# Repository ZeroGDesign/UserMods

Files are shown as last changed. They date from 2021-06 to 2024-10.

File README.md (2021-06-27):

# ZeroG repository

Welcome to the [ZeroG](https://github.com/ZeroGDesign/Mercury) github repository. This is a place to share your awesome mods for the Mercury One and find useful resources from other ZeroG community members.

Check the  [`Mercury_One`](./Mercury_One) and [`Slicer_profiles`](./Slicer_profiles) folders for mods that apply to the [Mercury One](https://zerogdesign.github.io/index.html).

If you want to contribute to this repository check step by step guide in [How to contribute](./docs/how_to_contribute.md)

<a href="https://discord.com/invite/gzJP2s8" target="_blank">Discord Shield</a>

<a href="https://www.buymeacoffee.com/dutchdude" target="_blank">Buy Me A Coffee</a>

ZeroGDesign/UserMods is licensed under the
GNU General Public License v3.0<br><br>


Credits to [VoronDesign/VoronUsers](https://github.com/VoronDesign/VoronUsers)

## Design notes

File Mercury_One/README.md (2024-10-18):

# Mods

Printer mods for ZeroG 3D printers
Remember to update this README when uploading new mod!

## Directory structure

Create a folder containing your name (without spaces) and create a folder for your mod(s).

Suggested directory layout for your mod:
- `creator_name/`
  - `mod_name/`
    - `README.md` with a description, optionally build instructions and required parts
    - `stl/` folder with stereolithographical models, oriented correctly for printing
    - `cad/` folder with original design files (STEP, F3D, Scad, etc.) (optional)
    - `doc/` folder with supported documentation (optional)
    - `images/` folder with screen shots/renders/etc.

## Table structure

Update the following table with the information about your mod:
- Your name
- A link to your sub-folder
- A short description of your mod
- The build difficulty:
  - `:green_heart:` for :green_heart: (Easy)
  - `:blue_heart:` for :blue_heart: (Intermediate)
  - `:heart:` for :heart: (Advanced)

like so:
`
| Creator | [Mod title](link) | Description | Difficulty `

---

| Creator | Mod title | Description | Difficulty
| --- | --- | --- | --- |
| *creator_name* | [*Mod Title*](./creator_here/mod_folder_name) | *Example description (short).* |:green_heart::blue_heart::heart:
| ZeroG | [Spool Holder](./ZeroG/Spool_holder) | Its a spool holder... Its holds spools? | 💚
| aepkolol | [rPi 3.5 LCD mount](./aepkolol/rPi-3.5-LCD-mount) | Adafruit 3.5" TFT screen on the front | 💚
| bertoo1337 | [AfterBurner fan shroud](./bertoo1337/AfterBurner_fan_shroud) | Mercury branded fan shroud for the Voron AfterBurner toolhead | 💙
| cncplasticfactory | [EVA KW10 X-axis endstop and bumpstop](./cncplasticfactory/EVA_KW10_X_endstop) | An X-axis endstop mount and bumpstop to use a KW10 microswitch with the EVA hotend | :green_heart:
|  | [KW10 enlarged Y-axis endstop mount](./cncplasticfactory/KW10_enlarged_Y_mount) | A modified and slightly enlarged Y-axis endstop mount for use with KW10 microswitches | :green_heart:
|  | [MGN12 Y-axis bumpstop endcaps](./cncplasticfactory/MGN12_linear_rail_bumpstop_caps) | Delightful bumpstops caps for Y-axis MGN12 linear rails | :green_heart:
| djsplice | [EVA - Biqu H2 Mount](./djsplice/EVA-Biqu-H2) | EVA Faceplate and fan shroud for the Biqu H2 hotend/extruder | 💚
|  | [Static Cooling System](./djsplice/SCS) | Static Cooling System for the Mercury 1.1 based on VzBoT RSCS system | 💚
| maze | [2020 endcap](./maze/2020-endcap) | Zero G branded 2020 endcap | :green_heart:
| OhDeeEsTee | [Inverted XY Bridge](./OhDeeEsTee/Inverted_XY_Bridge) | inverted cable chain mount | :green_heart:
| Rudra | [X Extrusion Squaring Tool](./Rudra/X_Extrusion_Squaring_Tool) | Simple tool to square the x extrusion to the frame | 💚
|  | [Belt Tensioning Tool](./Rudra/Belt_Tensioning_Tool) | Simple tool to ensure a 150mm distance from idler to idler for easy belt tensioning | 💚
| DrPeterPlastic | [Wago4-Mount](./DrPeterPlastic/Wago4-Mount-Hydra)  | Mount for 4 Wagos on Hydra | 💚
| Vengeful | [Klicky Mount](./Vengeful/Klicky_Bracket) | E5 Plus Mounting Bracket for Klicky mod| 💚
|  | [Standalone Knob Tensioner](./Vengeful/Standalone_Knob_Tensioners) | Knob Tensioners for Mecrury Printers| 💙
| hrt_plk | [MGN9H gantry](./hrt_plk/gantry-mgn9h) | Custom parts to replace y axis from MGN12 to MGN9 | 💚
| JohnJohnGib | [ZeroG frame corner braces](./Tomadoggy/ZeroG_Frame_Braces) | Its a spool holder... Its holds spools? | 💚

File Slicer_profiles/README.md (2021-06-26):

# Slicer profiles

Slicer profiles for ZeroG 3D printers, separated by slicer.
Remember to update this README when uploading new slicer configurations!

## Table structure

Update the following table with the information about your mod:
- Your name
- A link to your sub-folder
- A short description of your slicer config
- The printer compatibility. Use `:heavy_check_mark:` for :heavy_check_mark: and`:x:` for :x:

like so:
`
| Creator | [Config Title](link) | Description | :x: | :x: | :x: | :x: |`

---

| Creator | Config title | Description | PrusaSlicer | SuperSlicer | Cura | Simplify3d|
| --- | --- | --- | --- | --- | --- | --- |
| DutchDude| [SuperSplicer high speed](./DutchDude) | Personal config high speed quality parts | :x: | :heavy_check_mark: | :x: | :x: |

---

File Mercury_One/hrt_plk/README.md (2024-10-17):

## Gantry MGN9H rails
  - Redesigned from original MGN12H
  - 4 bolts
  - successfully assembled

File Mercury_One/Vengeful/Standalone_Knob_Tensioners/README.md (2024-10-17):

# Standalone Knob Tensioners

This mod is designed to provide a simple and sturdy solution for tensioning belts on the Ender 5 Plus(Need confirmation for the Ender 5) Mercury 1 and Mercury 1.1 Systems

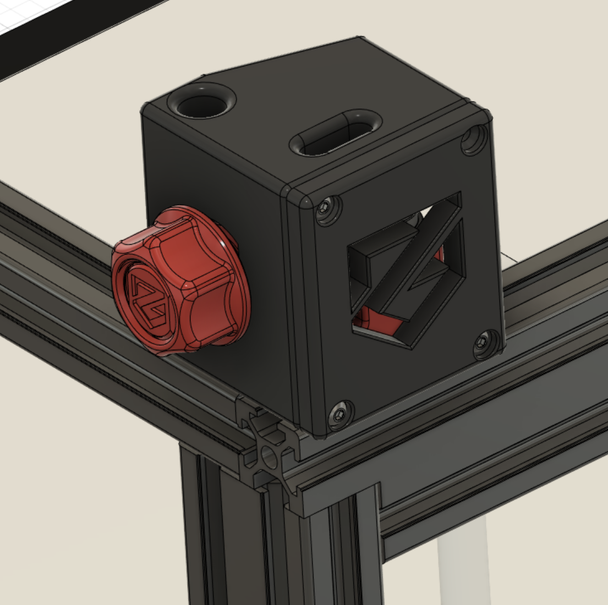
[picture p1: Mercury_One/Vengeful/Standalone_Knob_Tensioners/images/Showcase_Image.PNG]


## Description

This Mod is derived from the enclosure project I am currently working on (Jan-2023). In order to provide a version that can be used by the entire Mercury community. I have forked the design and will upload the enclosure version once I am done. This was inspired by the Voron V0. This provides a sturdy solution for tensioning your belt while maintaining a design that allows clearance for an enclosure.  

## Dependencies

* **Please print in ABS or ASA**
* Due to the tight clearances of a part like this, I recommend this part be printed on a properly calibrated printer
* I **Do not** recommend scaling the parts via a slicer as you may have issues with fitment

## Bill of Materials
Item Name | Quantity | Notes
| :--- | :---: | :---
M5x12mm BHCS | 2 | Needed for Rear Mount
M5x25mm BHCS | 2 | Needed for Inside Mount
M3x6MM BHCS | 8 | Needed to secure lid
M3x4mmx5mm Heatset Inserts | 8 | Needed to secure lid
M5 T-Nut | 6 | You should have at least 4 existing T-nuts from the Original BOM
M5x20mm SHCS | 2 | From Original BOM
M5x30mm PIN | 2 | From Original BOM
M5x1mm Shim | 4 | From Original BOM
F695 Bearing | 4 | From Original BOM

## Installation

### Step 1 - Install Heatset Inserts

* Install the Heatset inserts with a soldering iron for both the Left and Right Frame printed parts
* Total amount of Heatsets to install is **8**
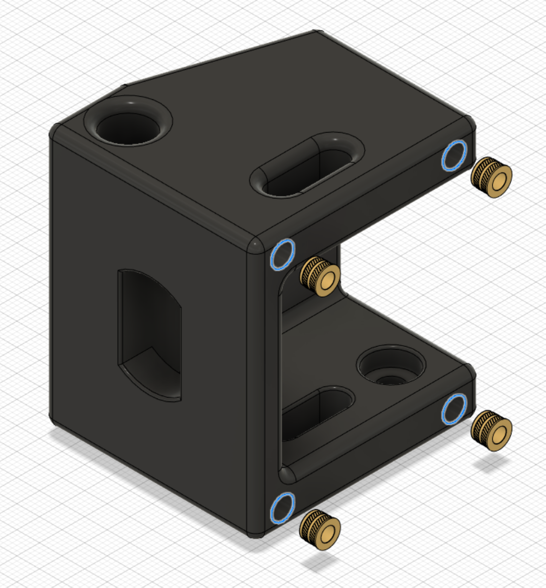
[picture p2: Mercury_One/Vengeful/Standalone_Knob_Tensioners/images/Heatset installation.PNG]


### Step 2 - Mount Frame to Extrusions

* Install the T-Nuts on both sides of the extrusion frame
* Total amount of T-Nuts to install is **6**
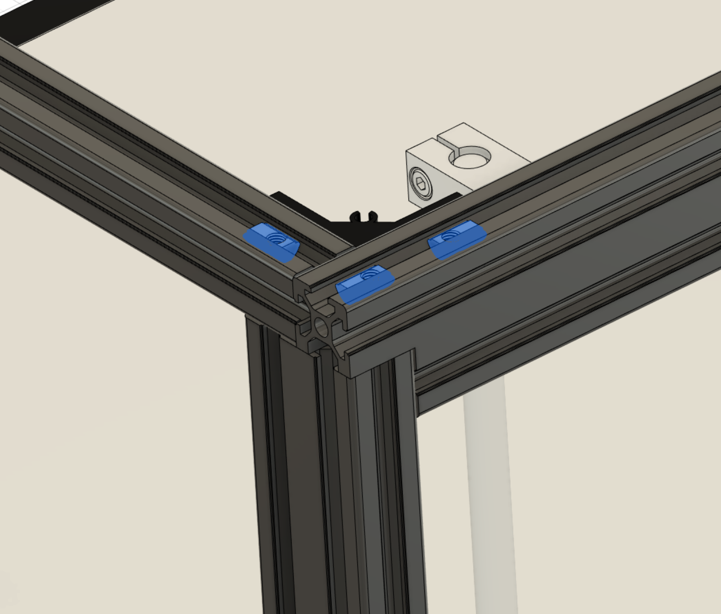
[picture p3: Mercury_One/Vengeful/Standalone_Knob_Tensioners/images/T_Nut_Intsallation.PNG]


* Install the M5x12mm BHCS at the Rear Mount hole
* Install the M5x25mm BHCS at the Inside Mount hole (This is a longer bolt to provide more structural rigidity)
* Repeat these steps on the other side as well
* Total amounts 
   * M5x12mm BHCS quantity of **2**
   * M5x25mm BHCS quantity of **2**
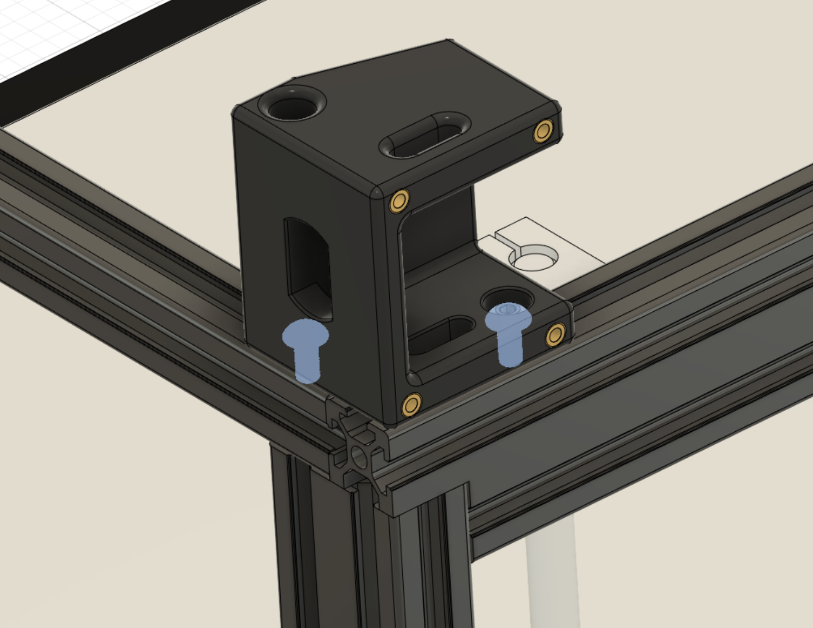
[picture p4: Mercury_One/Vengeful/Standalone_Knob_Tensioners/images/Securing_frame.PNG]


### Step 3 - Install Bearing Stack

* Install the bearing stack as prescribed in the original instructions for the Mercury Printers
* At this time you should insert the M5x20mm SHCS since the bolt will be held captive once the tensioner is inserted to the frame
* Repeat this process on both sides
* Total amounts 
   * M5x20mm SHCS quantity of **2**
   * M5x30mm PIN quantity of **2**
   * M5x1mm Shim quantity of **4**
   * F695 Bearing quantity of **4**
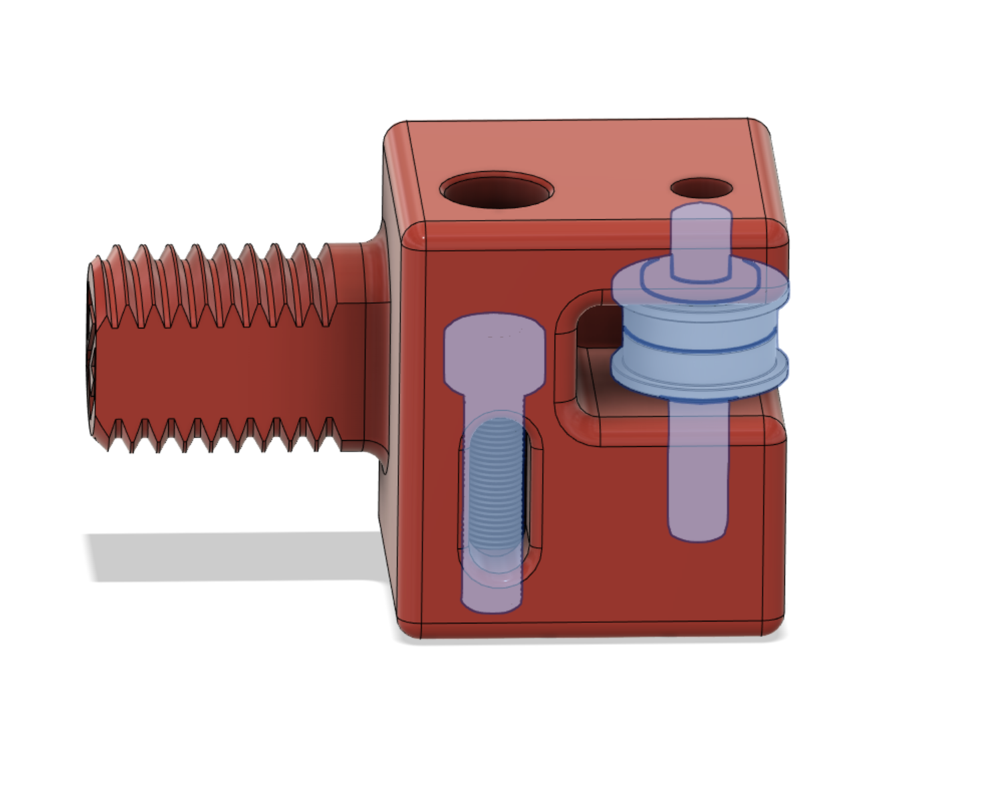
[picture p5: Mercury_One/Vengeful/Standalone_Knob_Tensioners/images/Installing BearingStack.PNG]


### Step 4 - Install Belt

* If this is a new build, follow the steps prescribed in the original instructions for the Mercury Printers
* if this is a retrofit, you will need to install as pictured below
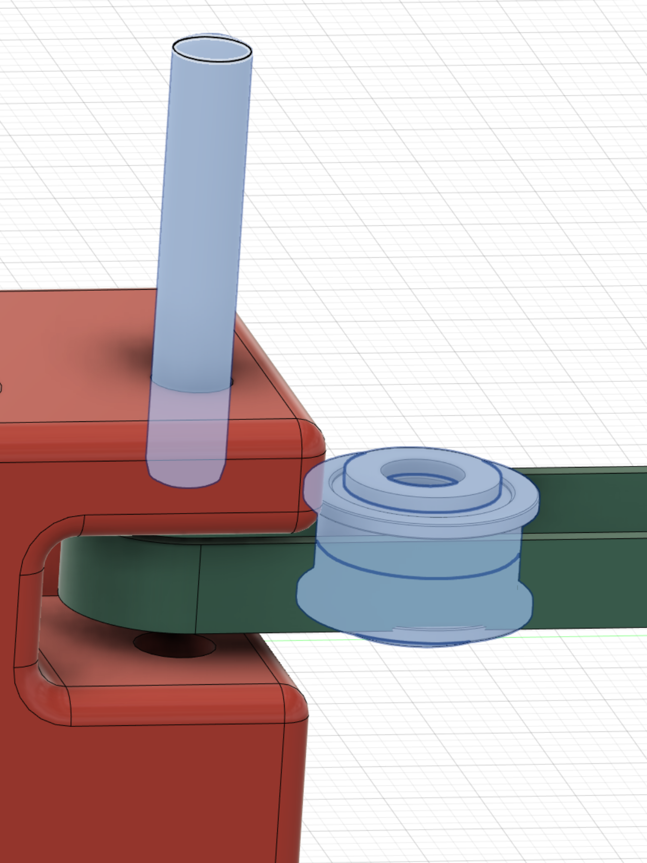
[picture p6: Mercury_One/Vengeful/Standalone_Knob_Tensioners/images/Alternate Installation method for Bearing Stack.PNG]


### Step 5 - Install Tensioner

* Slide in the tensioner to the frame
* Attach the M5x20mm SHCS to the T-Nut but **Do Not** fully tighten
* **Note** - the M5x20mm SHCS may catch on the initial hole
   * The Stadium Shaped Slot can be used to lift the bolt
   * This slot also exists in case you need to uninstall the tensioner - *since it will be captive once fully inserted*
   * A pick and hook can be used for this or a small screwdriver
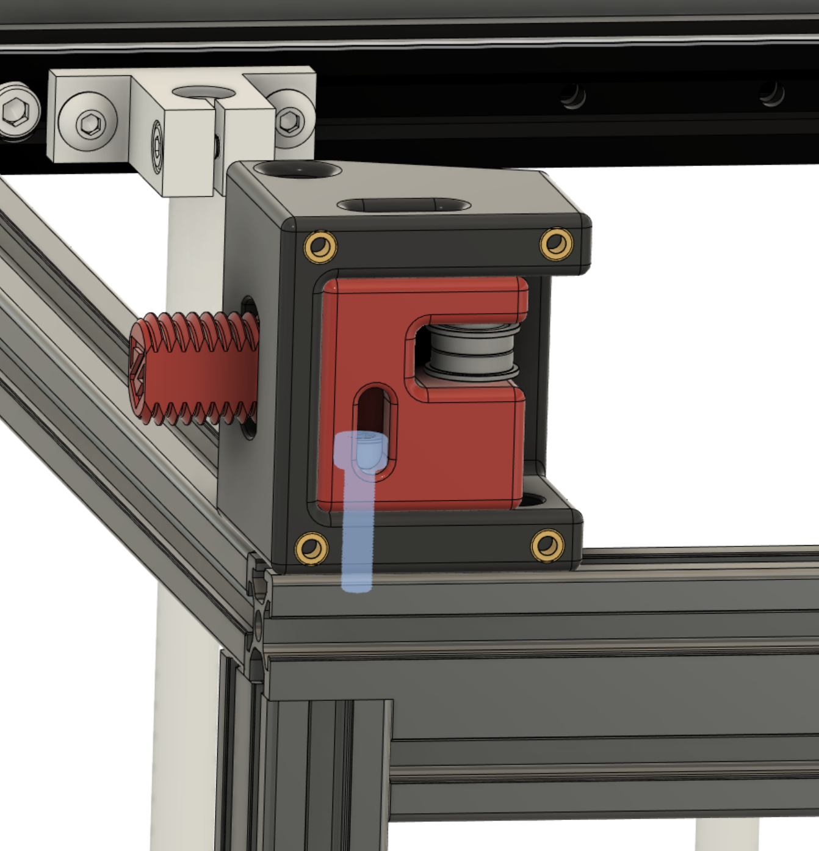
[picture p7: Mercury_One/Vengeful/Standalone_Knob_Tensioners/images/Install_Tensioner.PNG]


### Step 6 - Install Knob

* Install the knob but **Do Not** fully tighten until everything is installed 
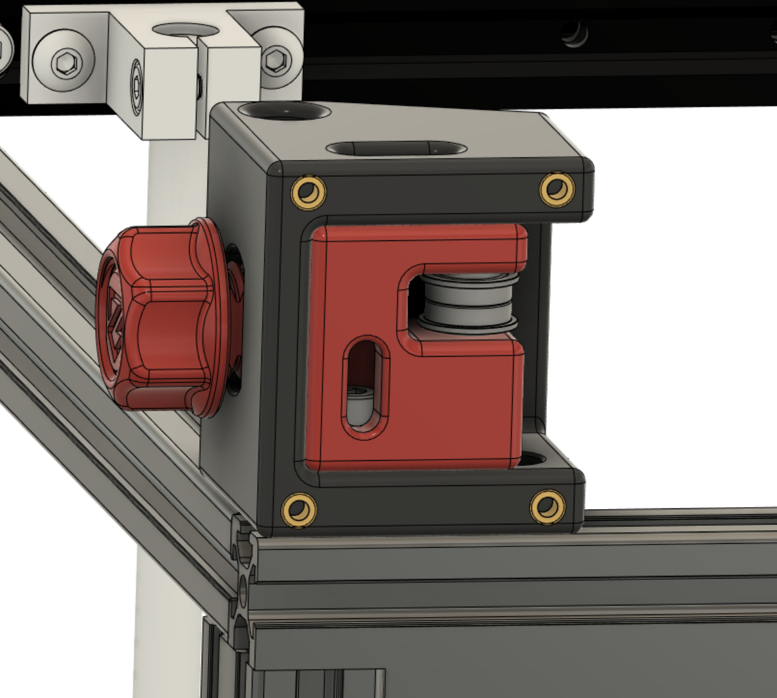
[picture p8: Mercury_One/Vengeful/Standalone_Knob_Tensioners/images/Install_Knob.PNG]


### Step 7 - Install Lids

* Install the lids on the sides of the frame
* Use the M3x6MM BHCS screws to secure the lids
* Total amount of M3x6MM BHCS screws to install is **8**
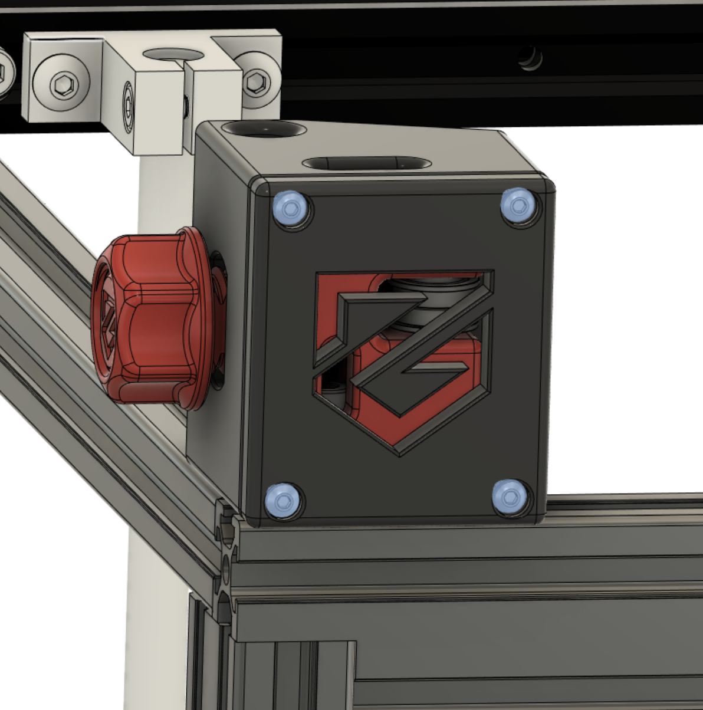
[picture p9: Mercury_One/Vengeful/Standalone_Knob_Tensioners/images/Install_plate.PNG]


## How to use

* Tension using the Knob
    * Ensure you are tensioning equally on both sides i.e 1/8th turn on each side simultaneously
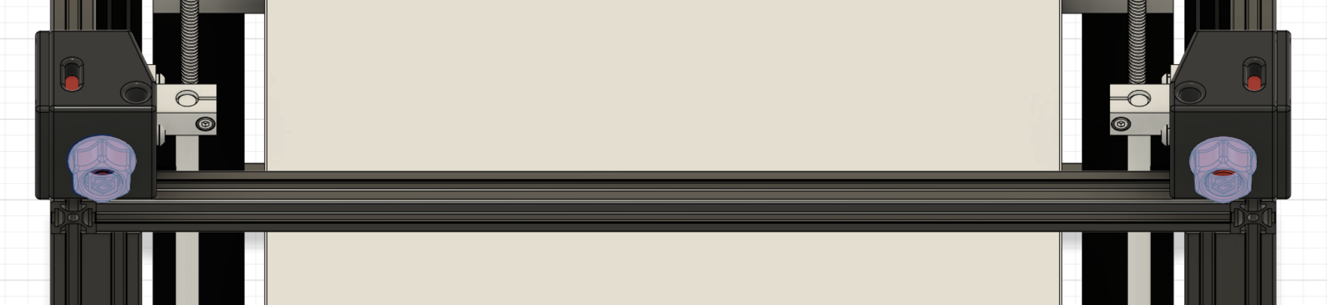
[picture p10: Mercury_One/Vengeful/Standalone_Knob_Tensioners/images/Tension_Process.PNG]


* Lock using the internal bolt inside the Stadium Shaped Slot
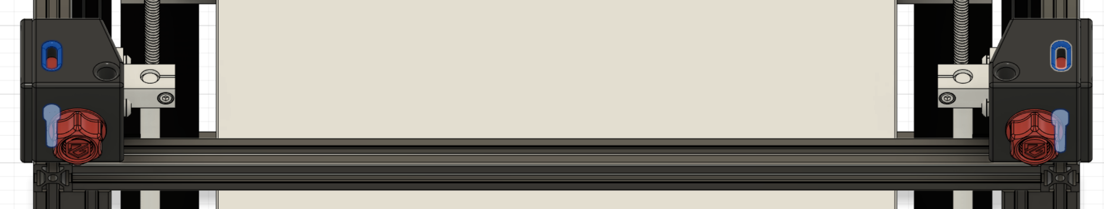
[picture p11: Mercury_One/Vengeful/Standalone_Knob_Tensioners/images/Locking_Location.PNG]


## Help

* Please reach out to me directly on discord if you have any issues or suggestions for this Mod 

## Authors

Vprince099 aka Vengeful Discord - Vengeful#8648

## Version History
    
* 0.1
    * Initial Release

## License

This project is licensed under the GNU GENERAL PUBLIC LICENSE - see the LICENSE.md file for details

## Acknowledgments

* ZeroG - Original Towers used to expand upon [Link to Project](https://github.com/ZeroGDesign/Mercury.git)
* Voron Design - V0 Team for Knob and Thread Appendage [Link to Project](https://github.com/VoronDesign/Voron-0.git)

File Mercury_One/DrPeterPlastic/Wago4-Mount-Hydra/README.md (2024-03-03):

Mount for 4 Wago connectors instead of 3

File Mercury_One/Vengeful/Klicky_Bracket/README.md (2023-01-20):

Intro:

This is dsigned for the Ender 5 Plus on the Mercury One System using a Stealthburner

Materials:

  M5x10 BHCS Q=2

  M5 T-Nut Q=2

  M3x4x5 Heatset Insert Q=2

Credit:
  
This is meant to be used with Klicky by jlas1 https://github.com/jlas1/Klicky-Probe.git

Images - 
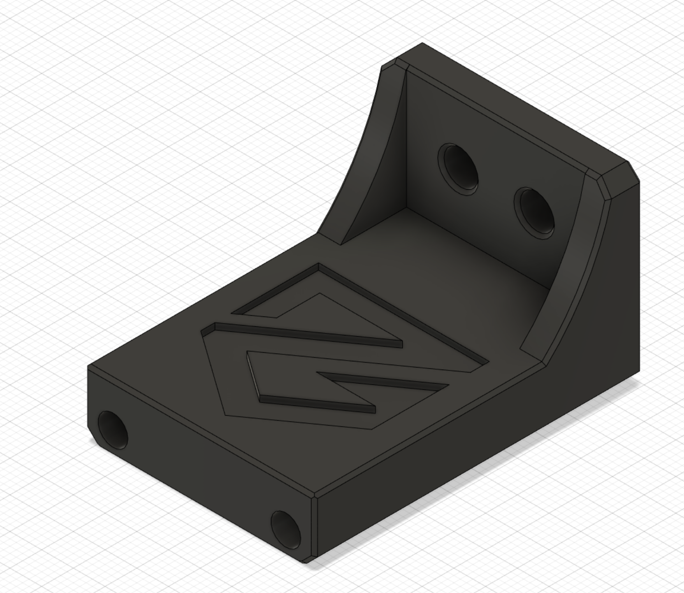
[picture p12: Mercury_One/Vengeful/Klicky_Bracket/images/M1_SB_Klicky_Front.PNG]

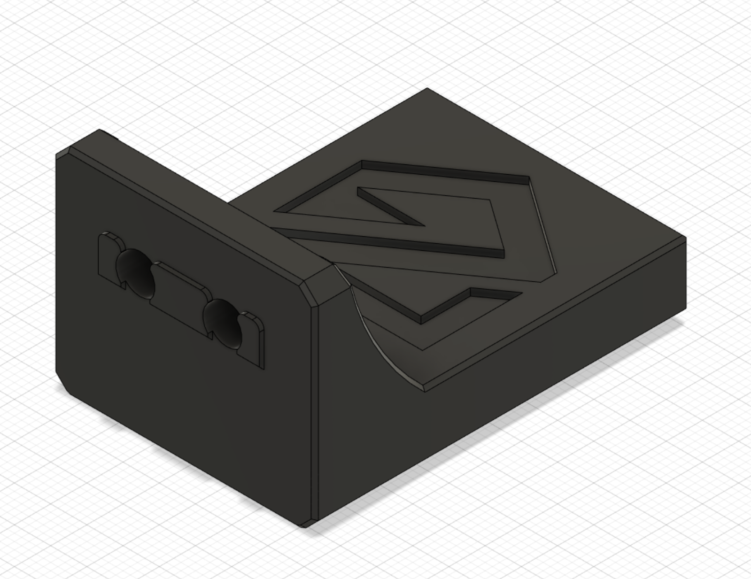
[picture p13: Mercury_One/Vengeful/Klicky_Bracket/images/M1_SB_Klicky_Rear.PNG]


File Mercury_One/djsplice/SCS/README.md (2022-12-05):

# Super Cooling System
This work is based on the [VzBoT RSCS system](https://grabcad.com/library/rscs-for-vzbot-1). Big thanks to the VzBoT crew, especially [Simon Vezina](https://grabcad.com/simon.vezina-2) for providing all of the CAD drawings and awesome videos for information, inspiration, and acceleration!

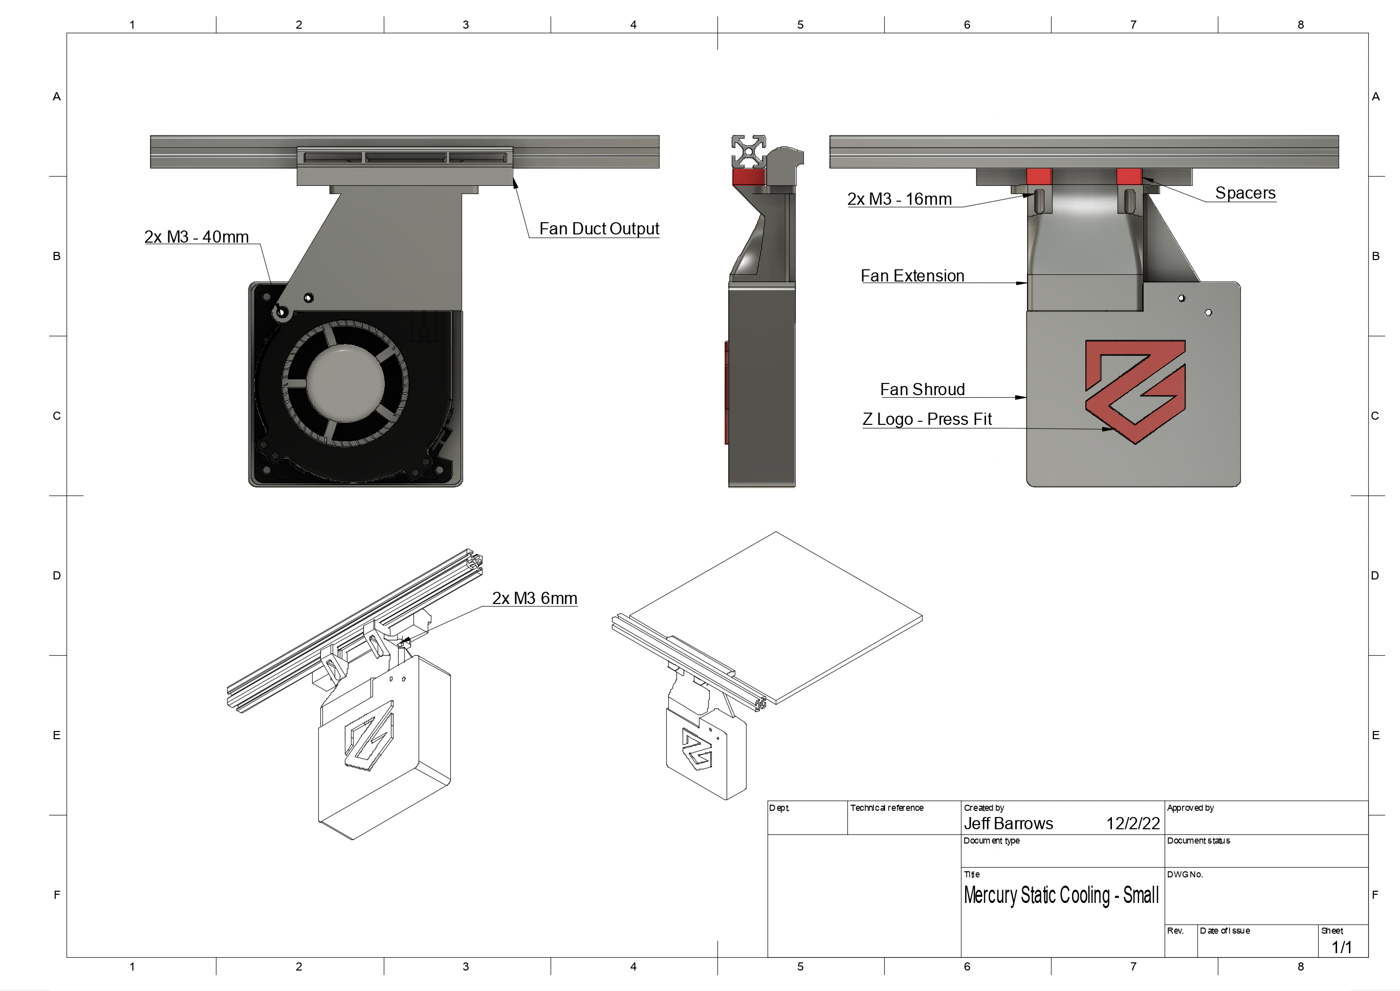
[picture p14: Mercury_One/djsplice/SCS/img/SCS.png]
Much SCS


## Release History
* 12/04/22 - Improved fan bracket airflow, and eliminated the need for the extension. Made shorter duct and increased inner cavity for improved airflow. Added a 'press-fit' Z for some flair.
* 7/11/22 - Updated fan bracket and shroud to cover more of the fans output. Increase overall fan bracket thickness improving mounting stability. Thanks to dansxmods#0246 (ZeroG Discord Server) for the suggestion!
* 5/26/22 - Initial Release

## What's SCS?
This is a system that's meant to cool top layer 3D printed extrusions quickly, helping you up the brrrr with better quality prints.

### What's the problem?
I found that as I tried to print at the higher end of my printers mechanical and extruder capabilities inevitably my print quality would suffer.  Especially challenging were overhangs, even 45 degree outer layers, and models with short layer print times (smaller single parts).

I moved to a dual 5015 cooling setup (EVA) for my part cooling which helped though at higher volumetric flows (~17mm3/sec), certain model features would become problematic (Benchy bow sag, ~45-50 degree overhangs in vase mode would deform at moderate speed, etc... ).

After watching and tuning for these scenarios it became clearer that cooling solutions that travel with the hot end have their limits. I think the main challenge is in that when printing at low layer times (<3sec), the fan ducts are generally not providing adequate cooling to the parts top layer surface because the hot end cooling fan is directly focused over the traveling nozzle.

More science necessary, though I believe cooling time could be calculated for a given material - helpful in determining quality print speed.

### Why try the SCS?
**First** I want to mention that the only reason I have this cooling problem is largely due to the [Zero-G Mercury project](https://github.com/ZeroGDesign/Mercury). By converting my heretofore fairly well tuned Ender 5 Pro printing at ~75mm/sec into something more 'moderately dangerous' - currently approaching 350mm/sec and 40mms3 volumetric flow.

After watching the [VzBoT video](https://youtu.be/65FVQ1jArME) on cooling solutions I was convinced to try this myself.

My hypothesis is that by adding additional top layer cooling, you'll be able to achieve higher speed/higher quality 3D prints.

If you're game, help me evaluate!

## SCS Parts, Printing, Installation
All printed files are found in the STL folder, CAD files *soon

This design works for the Ender 5 Pro, just fits between the top 2020 extrusion and a 300mm bed. If you have a smaller bed, or the Ender 5 Plus it should fit, though for the plus it may be a bit too far away from the bed, or not provide great part coverage... Drop an issue in Github if you get a chance to test it!

You will need M3 screws, 2 fans, and the ability to print 15mm overhangs clearly - you can do it - or your money back!   

### Hardware
* 2x 120x32 centrifugal fans - make sure they match the voltage and pin configuration your board can work with!
 * Ability to crimp, solder, or otherwise connect the fans to your 3D printer controller board
* Various M3 bolts/nuts:
 * 2x 40mm bolts to affix fan and shroud to mount
 * 2x 6mm M3 bolts to connect the fan shroud to the fan extension
 * 2x 16mm M3 bolts to connect the entire system to the underside of 2020 Aluminum extrusion
* Roll In Spring T-Nuts for mounting the blower to the top 2020 extrusions-  - something like [these](https://8020.net/fasteningmethods/hardware/tnuts/rollin/rollintnutwithballspring.html)

### Printed Parts
I recommend using the the following print settings:
* 3 Perimeters and 4 bottom/top solid layers
* 40% infill

All printed parts are included in the STL folder - there are 5 parts:

* [Fan Duct.stl](stl/Fan_Duct.stl)
* [Z-Insert.stl](stl/Z-Insert.stl)
* [Fan Bracket.stl](stl/Fan_Bracket.stl)
* [Fan Shroud.stl](stl/Fan_Shroud.stl)
* 2x [Spacers.stl](stl/Spacers.stl)

### Installation
1. Thread the M3 6mm screws that will be used to attach the fan duct, let the screws protude slightly from the top so it's easier to mount the duct later. The screws will thread directly into the duct housing - no nuts necessary.
1. Insert the M3 16mm screws that will be used to mount the system to the underside of the 2020 extrusion, thread the t-nuts
1. Using roll-in t-nuts will allow you to tilt the duct and get them inserted under the 2020 extrusion
1. Center the duct so that it's in the middle of your print bed
1. Once the duct is hanging from the 2020 extrusions, insert the spacers between the the extrusion and the duct mount, and tighten the bolts
1. Mount the Fan Duct Output on top of the Fan Extension.
3. Mount the fan and the shroud

The base of Fan Duct Output should align with the base of your print bed - the idea is for the air to blow onto the top layer of your print, if it's too high above the bed, it won't be as effective.

You may need to adjust the height of the spacers to achieve optimal alignment for your printer.
[TODO] Add a few more spacer sizes to accommodate

### Klipper gcode macro example
Configure Klipper to control the fans and expose a GCode macro so it can be controlled by your slicer.

#### Klipper Fan configuration
```
[output_pin Bed-Blower-R]
# BED BLOWER RIGHT
pin: PD12
pwm: true

[output_pin Bed-Blower-L]
# BED BLOWER LEFT
pin: PD13
pwm: true
```

#### Klipper GCode Macro
```
[gcode_macro BED_BLOWER]
gcode:
    # Use a default fan speed to off - expecting an INT as input
    {% set S = (params.S)|default(0)|float %}
    {% if S > 0 %}
        {% set S = (S/100) %}
    {% endif %}
    SET_PIN PIN=Bed-Blower-R VALUE={S}
    SET_PIN PIN=Bed-Blower-L VALUE={S}
```

#### Klipper Custom M106 Macro
This macro will set your SCS Fans to the same value your slicer sets the part cooling fans to, making it more dynamic. There are probably some advantages to having an 'always on' static setting, vs a dynamically adjusted setting such as this.

```
[gcode_macro M106]
rename_existing: M106.1
gcode:
  M106.1 { rawparams }
  {% set bed_blower_speed = params.S|float * 100/255 %}
  SET_PIN PIN=Bed-Blower-R VALUE={ bed_blower_speed/100 }
  SET_PIN PIN=Bed-Blower-L VALUE={ bed_blower_speed/100 }
```

### SuperSlicer custom gcode integration
In order to automatically turn on the SCS fans at a specific layer height, you need to add some custom `Before Layer Change G-code` section under the 'Printer Settings' in SuperSlicer.

```
; Set SCS fans to 40% when you reach the 3rd layer
{if layer_num == 2} BED_BLOWER S=40{endif}
```

## Known Issues

### Fan Duct Outlet
* Lots of bridging in this print!!  I tried to keep the bridge distance low, around 15mm or so... It's a bummer, but hopefully it's doable.

### Fan Bracket
* There are only 2 points to connect the fan to the bracket and it isn't as secure as I'd like. I'll probably look to add another mount point and potentially strengthen the hole on the point of the triangle...

## Experiments
Here are some pictures of benchys printed using the same g-code, but with  different cooling solutions.

Slicer configuration
2 Perimeters, 3 Top/Bottom solid
.2mm layer height
18% gyroid infill
Internal Perimeter Speed 250mm/s - External - 125mm/s
Max Volumetric Speed 43mm/s

1. Single 5015 Part cooling Fans at 100%
1. Dual 5015 Part cooling Fans at 100%
1. Dual 5015 Part cooling fans at 100% plus SCS fans at 100%

My interpretation of these results:
* Short layer times require increased cooling capacity
* Certain features (like overhangs) will degrade more than others when cooling isn't sufficient
* Layer times and cooling requirements are correlated - faster layer times will require more Cooling
* Prints that have more surface area may have a bit more time to cool before the next layer is applied, however, nozzle based cooling solutions will be less effective because they are only in a position to cool a section for a very short amount of time (as the filament is extruded from the nozzle)
* Smaller prints can benefit somewhat from increased nozzle based cooling systems because the ducts are likely to cover more surface area of the print for a more sustained period of time. Unfortunately smaller parts will likely have very short layer times and nozzle based cooling will probably not be sufficient   

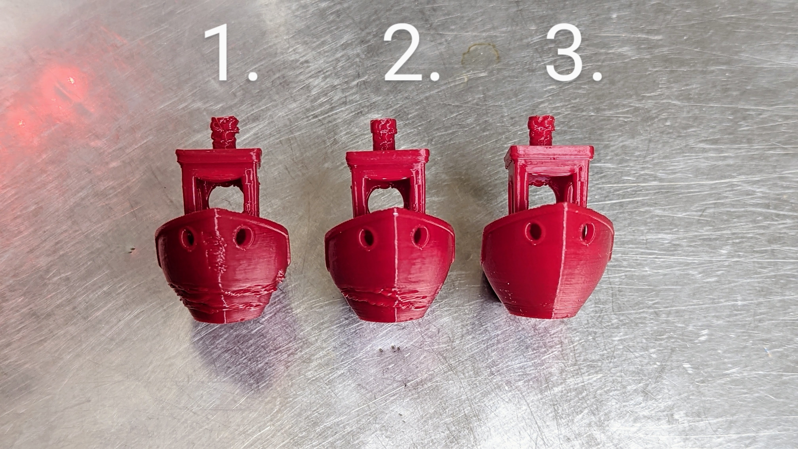
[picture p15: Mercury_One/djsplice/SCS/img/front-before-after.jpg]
Benchy Front View

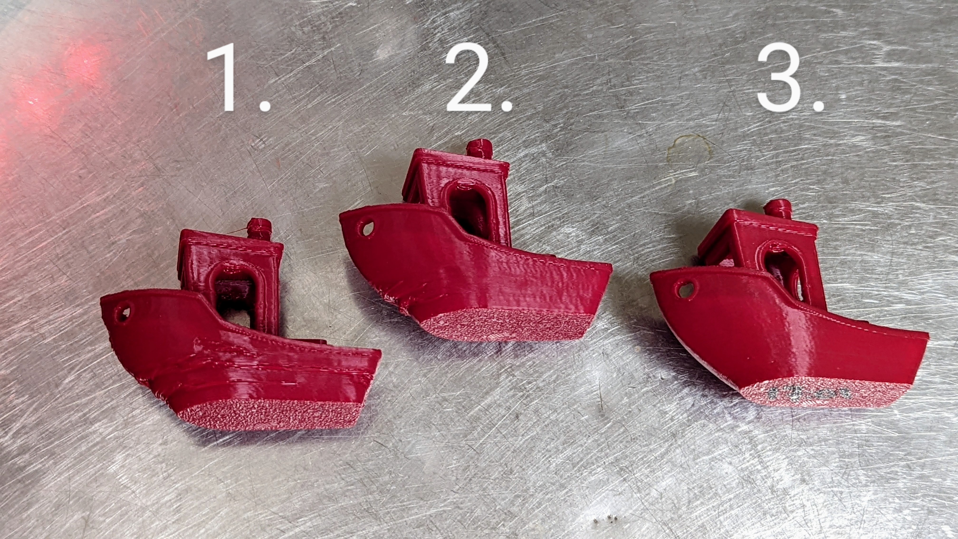
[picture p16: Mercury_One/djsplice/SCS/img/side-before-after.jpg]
Benchy Side View


### CFD Study
I found a nice [tutorial / overview](https://www.youtube.com/watch?v=Wun9EuVTV0w) from Teaching Tech that showed how to do some Computational Fluid Dynamics simulations using a site called [Simscale](https://www.simscale.com/). I quite literally have no idea if I'm using this tool correctly or not! With that said, it seems to provide some good visualizations of air flow, and reflects the changes I'd expect to see as I refined the CAD model.

Here is my [SimScale project](https://www.simscale.com/projects/djsplice/super_cooling_system_v2/), take the data for what it's worth - mostly for the neat visualization of airflow =)

It's been great to be able to make updates to a CAD model like this and run a simulation against the updated model to see if it has the intended effects - all before printing the part! Running the simulations take about an hour, so there's not tons of time savings, however, I do save quite a bit of filament!

#### V2 duct output design
Made some updates to the duct output in an attempt to better distribute the airflow across the bed, and keep it focused on the top layer of the print. It looks like the bed coverage has improved, perhaps at the cost of some velocity.  All good gains I think.

As much as I enjoy running simulations and updating CAD, I've decided to pause the iteration and get some real world print time under my belt with the current design as published here in GitHub.

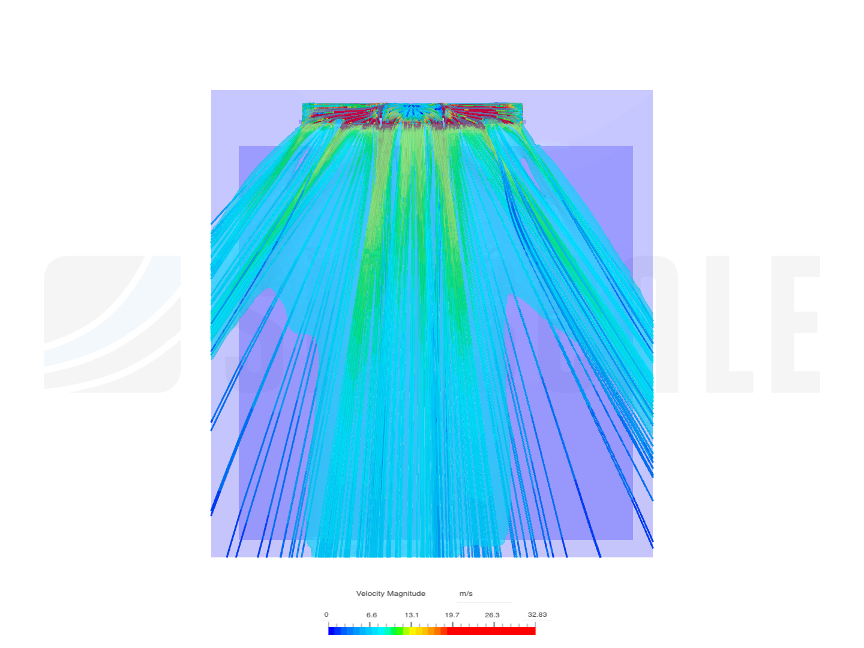
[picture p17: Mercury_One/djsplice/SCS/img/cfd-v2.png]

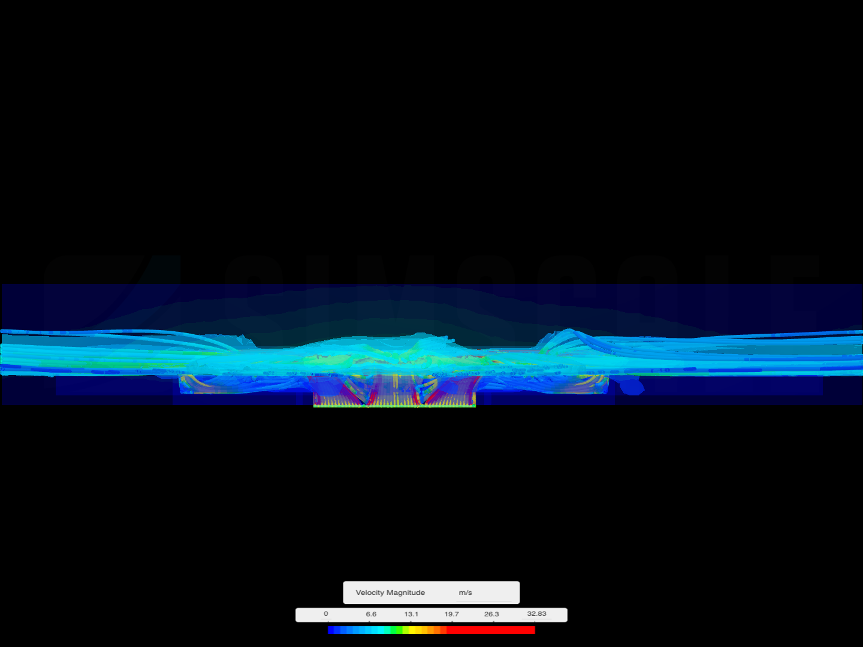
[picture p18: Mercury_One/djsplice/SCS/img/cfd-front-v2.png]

CFD v2 fan duct full plate

#### V1 duct output design
Some data to back up the physical observations (places hand in front of the vents). Looks like most of the air is flowing through the center of the duct, not much is getting to the outside edges...
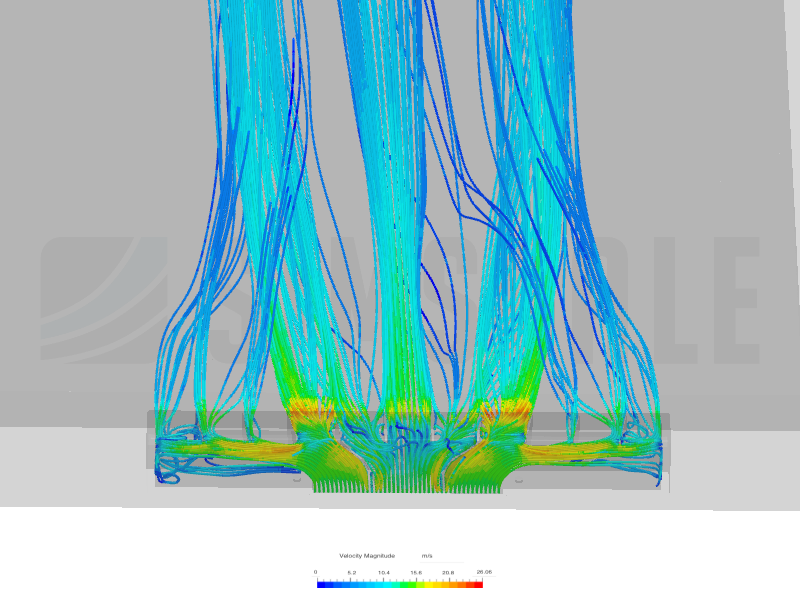
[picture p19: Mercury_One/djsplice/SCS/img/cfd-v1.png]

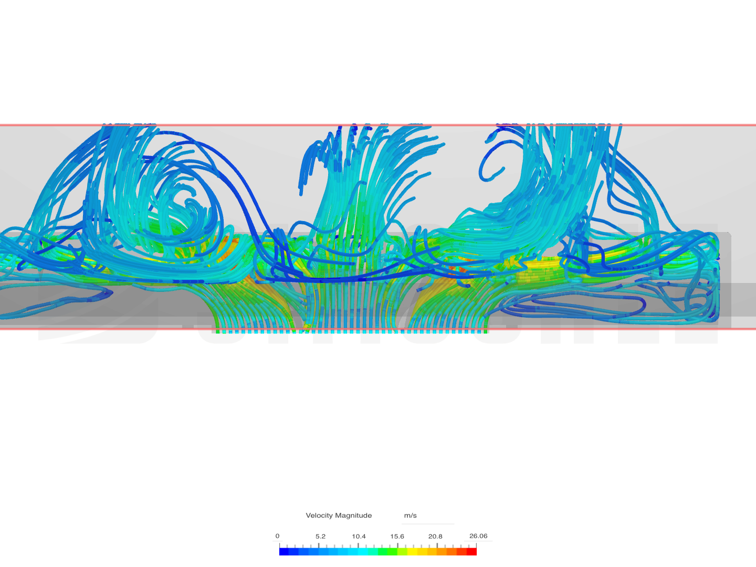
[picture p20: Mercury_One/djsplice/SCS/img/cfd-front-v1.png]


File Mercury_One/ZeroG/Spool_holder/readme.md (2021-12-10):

ZeroG Spool Holder by Häagen Dazs Pizza

spoolholder

| Printed Part | Quantity |
| --- | --- |
| LeftSpool | 1 |
| RightSpool | 1 |
| spoolholder_nut | 2 |
| spoolholder_short | 2 |

| Mechanical Parts | Quantity |
| --- | --- |
| 5/16 OR M8 threaded rod cut at 250 | 1 |
| 5/16 OR M8 nut | 4 |
| PC4 M10 Fittings | 2 |
| 25mm M3 screws | 2 |
| M3 Nut | 2 |
| 10mm M5 screw | 2 |
| M5 T-nut | 2 |

Creds to ‘butchja’ on Thingiverse for the universal threaded spool holder
https://www.thingiverse.com/thing:2070272

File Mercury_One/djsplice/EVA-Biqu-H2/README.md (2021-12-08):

# EVA mount for the Biqu H2 hot end / extruder

These were designed to work with the [Mercury One](https://github.com/ZeroGDesign/Mercury) conversion for an Ender 5. Rudra has made an [EVA universal faceplate](https://drive.google.com/drive/folders/1WeMnU41LHNeeJy4bnJhXC6Zqy8RPeaLE) based on the EVA v2 spec that works with the Mercury One belt paths.

This is a mount that connects the Biqu H2 hot end and extruder to the EVA Mercury faceplate, with fan duct to match.

The fan duct is loosely based on the official [EVA](https://main.eva-3d.page/) fan ducts. 'Loosely' in the fact that I'm a CAD n00b, and the official designs have much more thought/testing put into them compared to my functional yet hacky rendtion! ;)

## Images
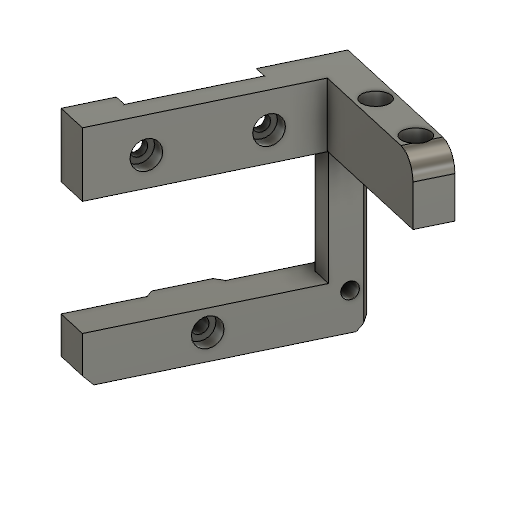
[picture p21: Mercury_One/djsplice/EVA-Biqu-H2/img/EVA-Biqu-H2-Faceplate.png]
Face Plate

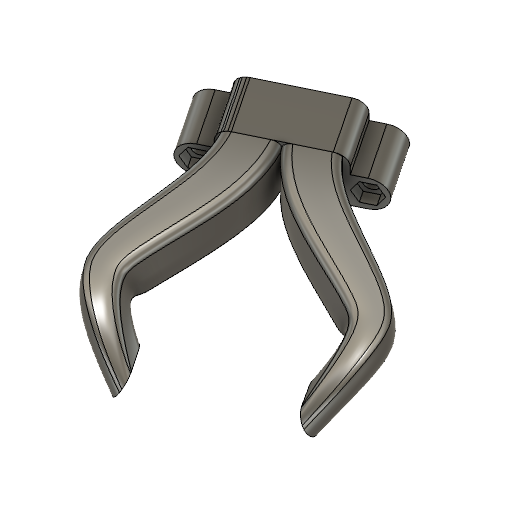
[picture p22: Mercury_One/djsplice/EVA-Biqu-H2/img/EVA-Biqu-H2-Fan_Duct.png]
Fan Duct


## Installation
* Download and print [EVA universal faceplate](https://drive.google.com/drive/folders/1WeMnU41LHNeeJy4bnJhXC6Zqy8RPeaLE), the Eva Biqu H2 mount, and the Fan duct.

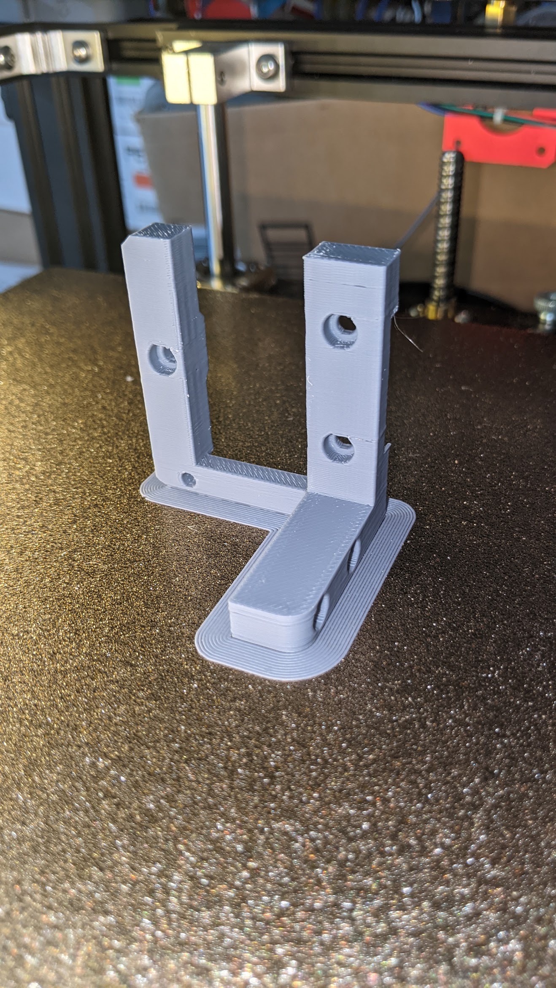
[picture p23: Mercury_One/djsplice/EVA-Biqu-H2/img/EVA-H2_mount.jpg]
Print orientation H2 Mount


* Attach the H2 faceplate to the EVA carriage using 3 M3 screws
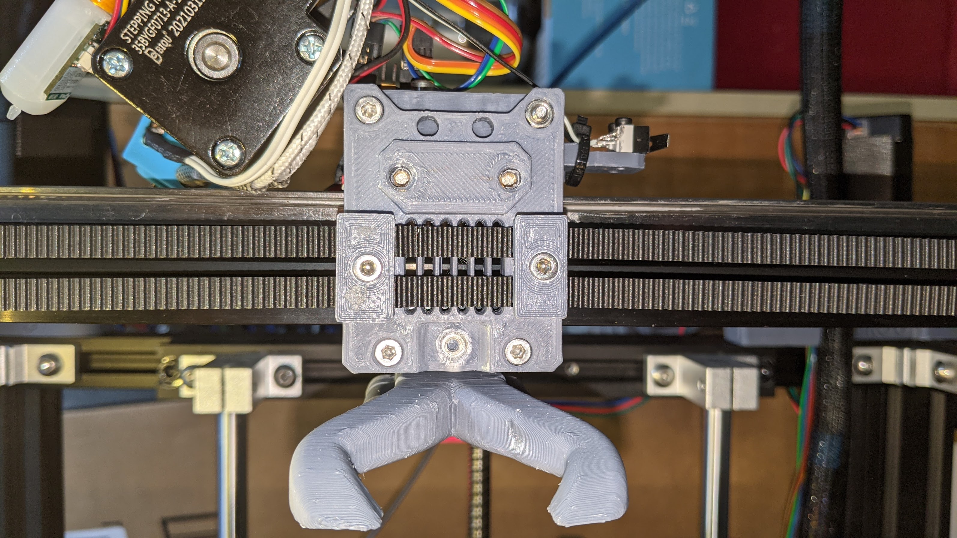
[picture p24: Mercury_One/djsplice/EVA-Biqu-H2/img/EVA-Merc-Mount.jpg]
EVA - Merc mount


* Attach the fan duct to the EVA carriage

* Attach the H2 to the faceplate via 2 screws on top of the H2, and one screw in the back.

Merc - H2 Faceplate mounted
Merc - H2 rear bolt

Installed

## Known Issues
1. I optimized the design to make it fairly easy to remove the H2 from the EVA carriage while providing good rigidity using 3 point connections (3 screws between the faceplate and the carriage, and 3 screws connecting the H2 to the faceplate). In initial iterations of this design, I'd tried connecting the H2 to the faceplate using only two screws, but vibrations at higher print speeds had negative effects on quality.

2. Because of the challenges with bolt clearances between the H2 mounts and the faceplate, the extruder is ever so slightly off center from the carriage. It's about 2mm off of center from the carriage which slightly interferes with the fan duct.

3. I had to design a new fan duct because existing mods didn't quite fit correctly for me. The current nozzle design sits pretty close to the build plate, 1mm clearance. Because of the H2 / carriage offset, the right side air duct seems to be a bit impeded. While there's more optimization to be had here, the fan duct works pretty well for general purpose prints.

4. I'm a CAD n000b - I make things that work for me, and by sharing them I hope other find utility in them as well!

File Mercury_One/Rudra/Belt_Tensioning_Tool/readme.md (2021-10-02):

Simple tool to aid when tensioning the belts on the Mercury One.
This ensures a distance of 150mm from idler to idler.

Print two and use as shown:



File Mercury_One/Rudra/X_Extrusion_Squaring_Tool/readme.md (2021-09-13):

Simple tool to square the x extrusion to the frame of the printer.

Can be used with belts on or off and while the printhead is installed (both afterburner and EVA). Also can be used during or after assembly of your Mercury One.

Uses 6 M5x8 or M5x10 bolts and 6 T-nuts (3 per tool).

Make sure to print out two of these.

Instructions for use:

1) Loosen belts and x extrusion mounting bolts.

2) Bolt onto the x extrusion:


3) Bolt onto the frame:


4) Tighten the x extrusion mounting bolts.

5) Remove from x extrusion and frame.

6) Done! Your x extrusion is now square to the frame!

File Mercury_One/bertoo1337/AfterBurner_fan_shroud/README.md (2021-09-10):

# AfterBurner fan shroud

This is a Mercury branded fan shroud for the [Voron AfterBurner](https://github.com/VoronDesign/Voron-Afterburner) toolhead.

AfterBurner Shroud

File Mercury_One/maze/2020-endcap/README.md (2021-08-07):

# 2020 end cap

Simple end cap for 20x20 profiles, type 5 (4.2mm bore) or type 6 (5mm bore).

Zero G 2020 endcap

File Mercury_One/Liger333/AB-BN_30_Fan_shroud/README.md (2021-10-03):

Use inlay from https://github.com/ZeroGDesign/UserMods/tree/main/Mercury_One/bertoo1337/AfterBurner_fan_shroud

Modified from https://github.com/VoronDesign/VoronUsers/tree/master/printer_mods/Badnoob/AB-BN



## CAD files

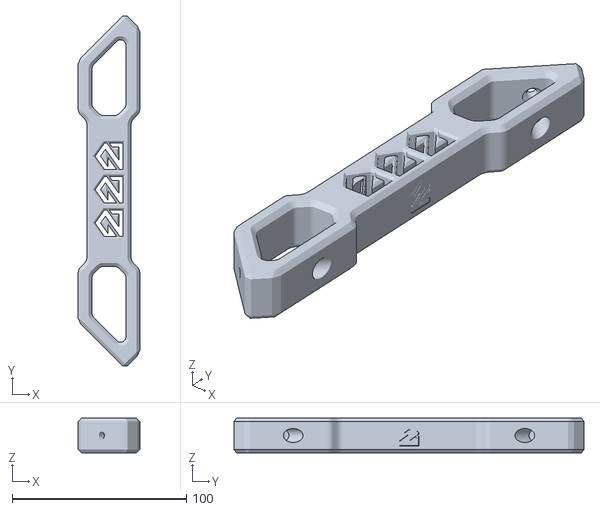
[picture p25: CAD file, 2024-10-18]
Mercury_One/JohnJohnGib/Frame Brace/Frame_Brace_M4_Zerog_Full.stl
35.4 x 200.9 x 20.0

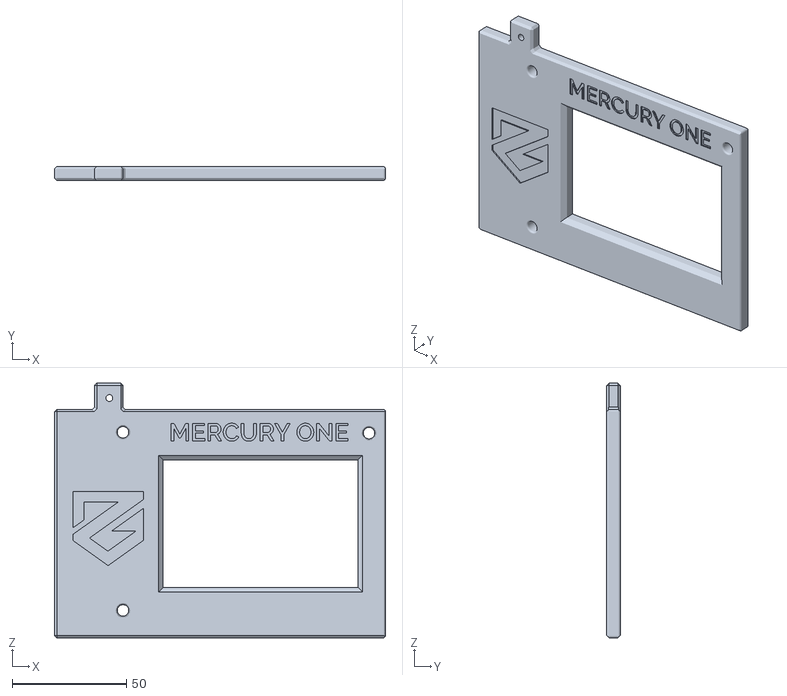
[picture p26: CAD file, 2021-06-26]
Mercury_One/aepkolol/rPi-3.5-LCD-mount/stl/LCD Thinger.stl
144.9 x 6.00 x 111.5

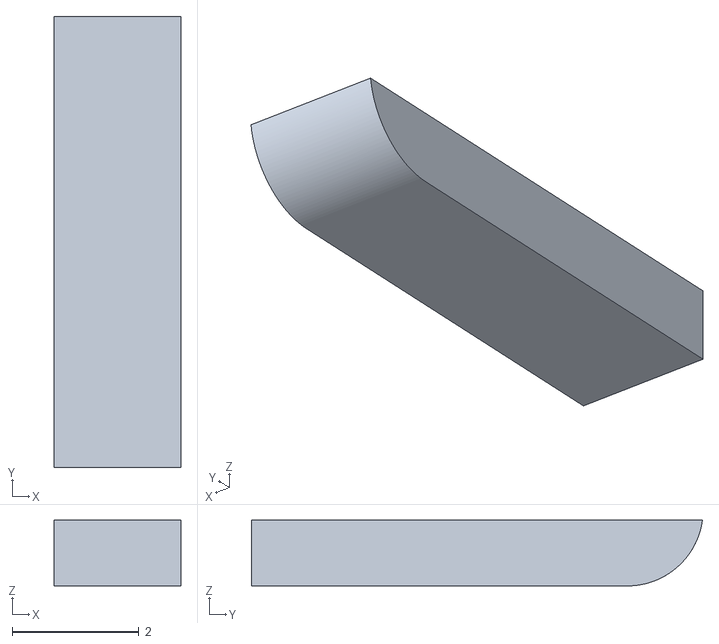
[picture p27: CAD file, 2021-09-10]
Mercury_One/bertoo1337/AfterBurner_fan_shroud/Inlay C1.stl
2.00 x 7.12 x 1.04

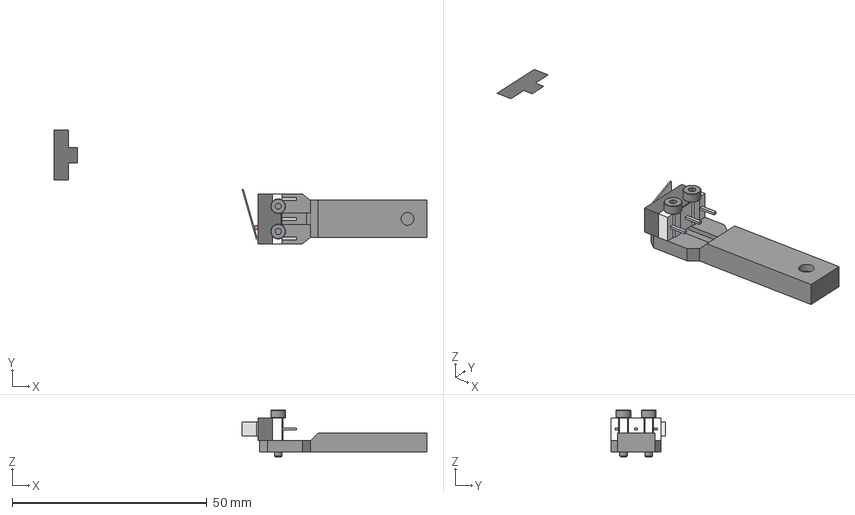
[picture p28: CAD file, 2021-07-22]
Mercury_One/cncplasticfactory/EVA_KW10_X_endstop/CAD/EVA_KW10_Endstop_Mount.step
95.9 x 29.2 x 12.0 mm
DIN 912 M2 10 mm x 2
EVA Top Endstop
Top
Pin (2)
Bottom
Pin (1)
Pin
Lever
Switch

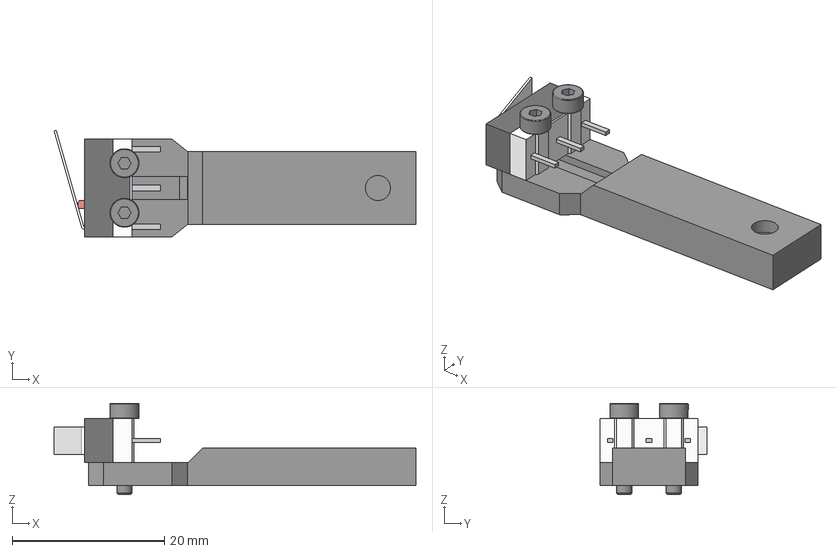
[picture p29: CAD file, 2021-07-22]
Mercury_One/cncplasticfactory/KW10_enlarged_Y_mount/CAD/KW10_Enlarged_Y_Endstop_Mount.step
47.5 x 14.0 x 12.0 mm
EVA Top Endstop
Top
Pin (2)
Bottom
Pin (1)
Pin
Lever
Switch
DIN 912 M2 10 mm x 2

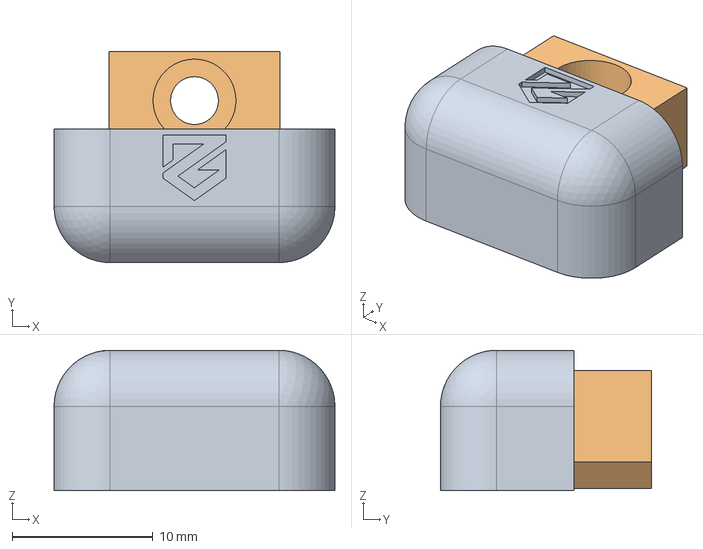
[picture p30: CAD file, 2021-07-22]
Mercury_One/cncplasticfactory/MGN12_linear_rail_bumpstop_caps/CAD/MGN12_linear_rail_bumpstop_cap.step
20.0 x 15.0 x 10.00 mm
Cover
Stopper

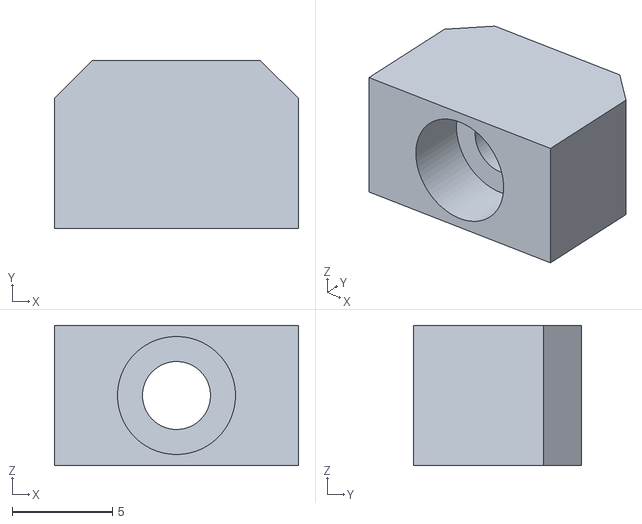
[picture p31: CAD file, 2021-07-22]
Mercury_One/cncplasticfactory/MGN12_linear_rail_bumpstop_caps/STLs/MGN12_stopper.stl
12.2 x 8.40 x 7.00

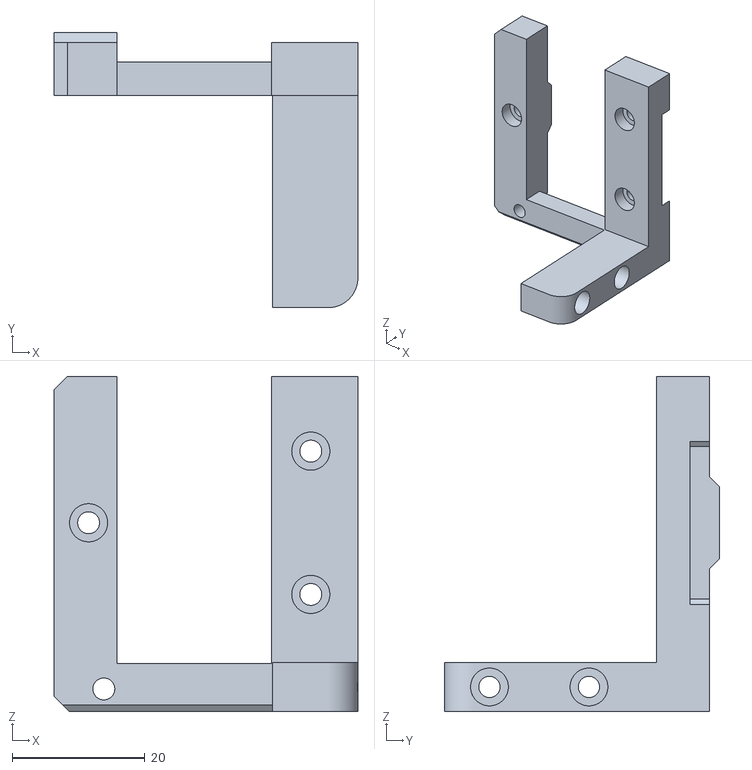
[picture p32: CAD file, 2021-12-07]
Mercury_One/djsplice/EVA-Biqu-H2/EVA-Biqu-H2-Faceplate.stl
45.8 x 41.5 x 50.5

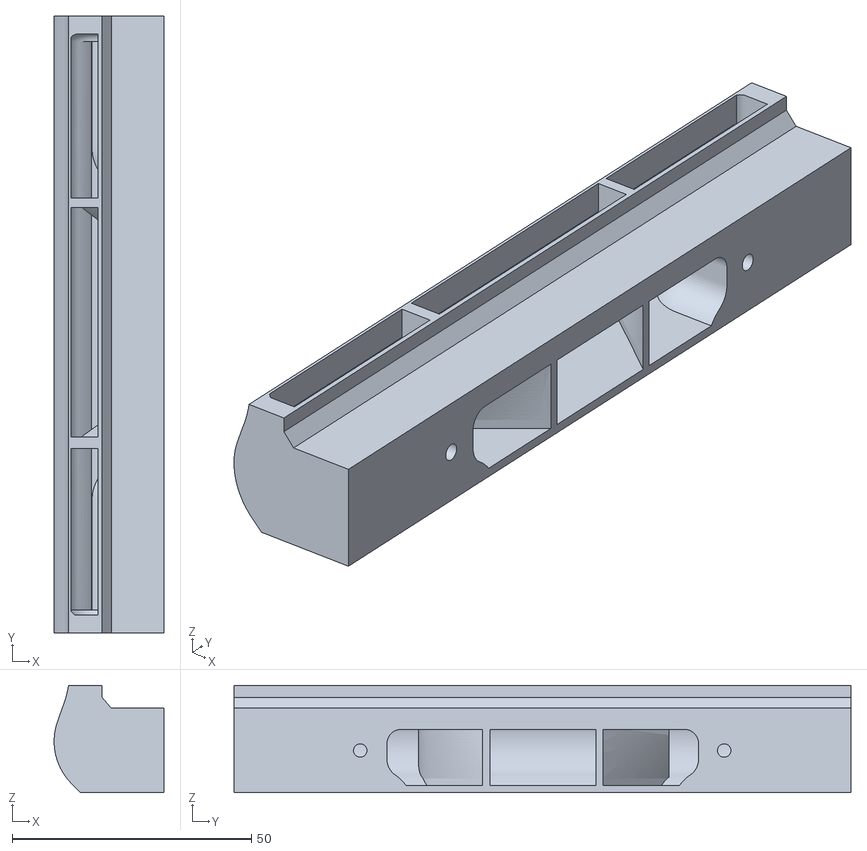
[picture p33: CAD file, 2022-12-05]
Mercury_One/djsplice/SCS/stl/Fan_Duct.stl
23.0 x 129.0 x 22.4

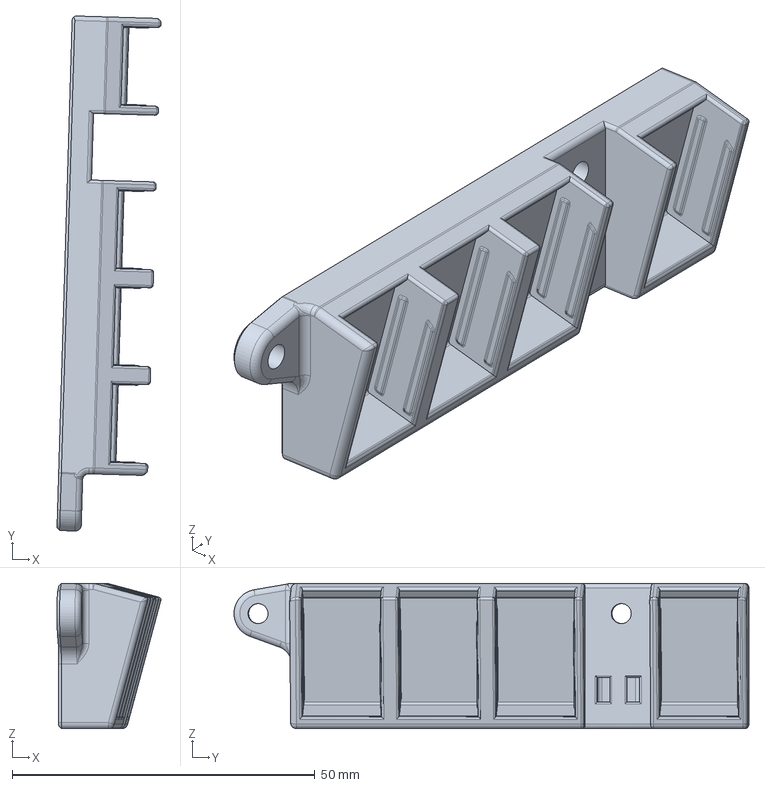
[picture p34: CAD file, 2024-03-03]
Mercury_One/DrPeterPlastic/Wago4-Mount-Hydra/cad/Wago4.step
17.2 x 85.0 x 24.0 mm

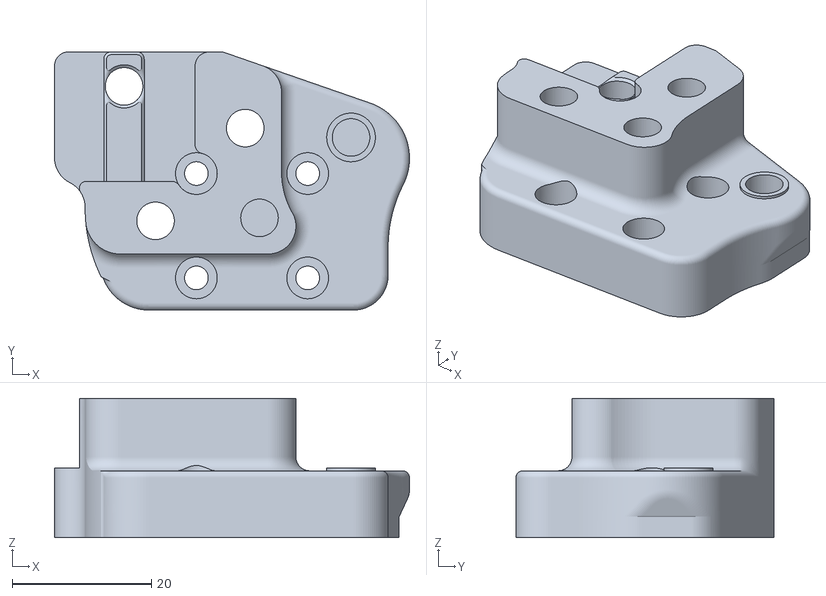
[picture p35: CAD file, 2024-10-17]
Mercury_One/hrt_plk/stl/gantry-mgn9h/y-l-9.stl
51.0 x 37.1 x 20.0

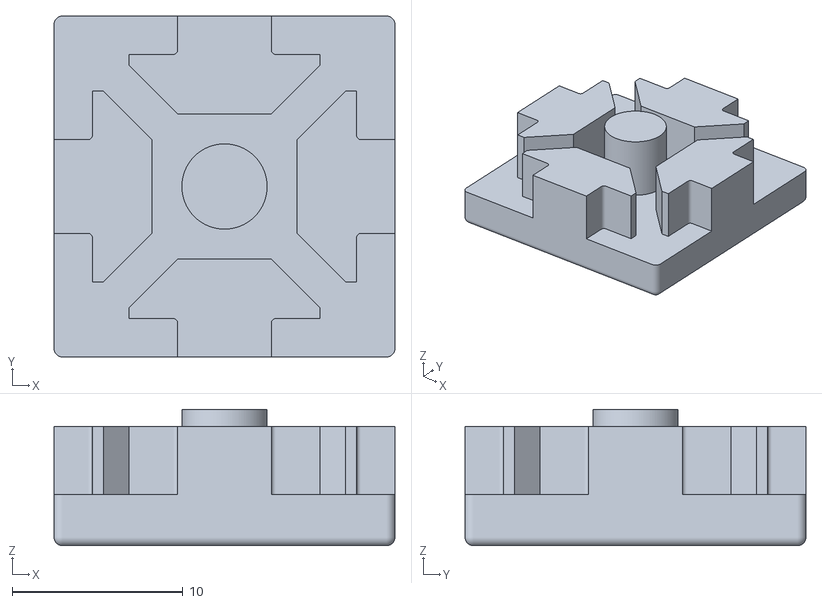
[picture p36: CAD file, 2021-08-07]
Mercury_One/maze/2020-endcap/ZeroG_2020_endcap_type_6.stl
20.0 x 20.0 x 8.00

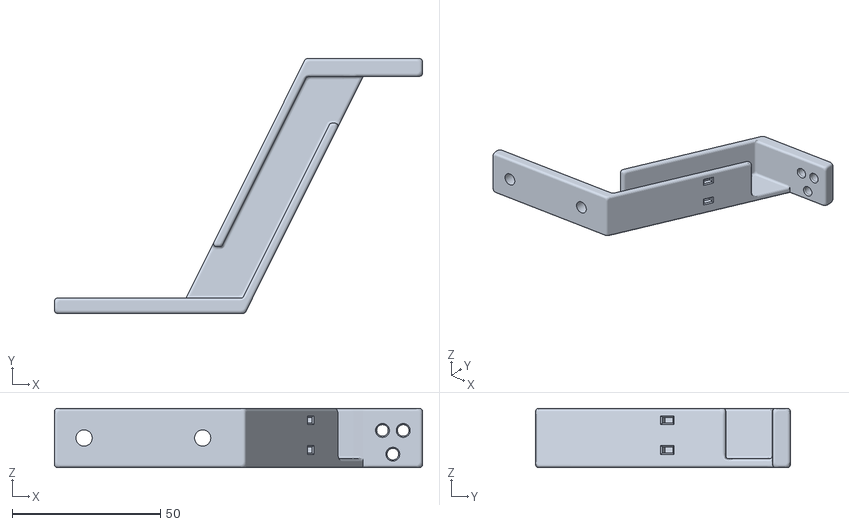
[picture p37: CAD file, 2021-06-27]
Mercury_One/OhDeeEsTee/Inverted_XY_Bridge/stl/underslung xy cable bridge.stl
124.2 x 86.0 x 20.0

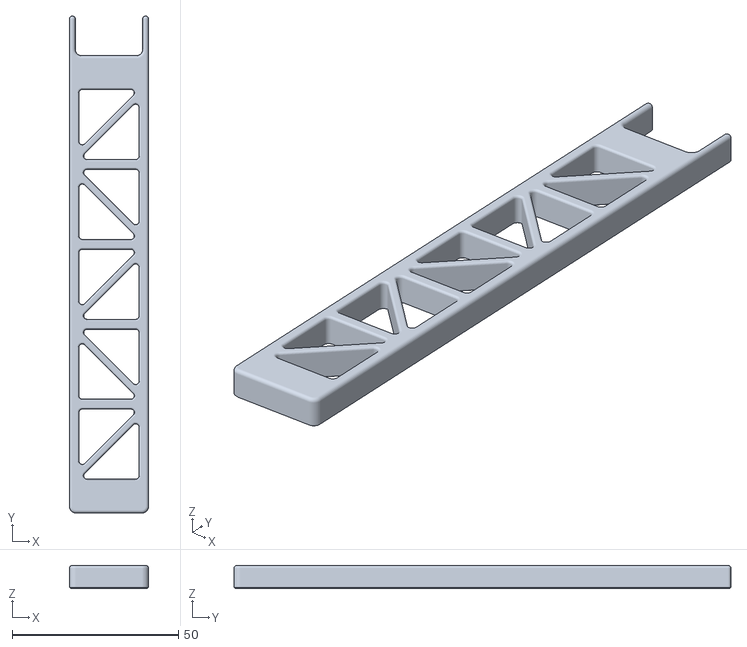
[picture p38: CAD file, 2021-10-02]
Mercury_One/Rudra/Belt_Tensioning_Tool/stl/belt_tensioning_tool_x2.stl
23.8 x 149.3 x 7.00

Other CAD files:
Mercury_One/justinr54321/EZABL Micro (8 mm) mount/AB_EZABL_micro.stl
Mercury_One/Rudra/X_Extrusion_Squaring_Tool/stl/X_Extrusion_Squaring_Tool x2.stl
Mercury_One/Vengeful/Klicky_Bracket/stl/M1_SB_KlickyProbe_Rear_mount_v1.stl
Mercury_One/Vengeful/Standalone_Knob_Tensioners/stl/Tensioner_Knob_x2(Accent_Color).stl
Mercury_One/Vengeful/Standalone_Knob_Tensioners/stl/left_tensioner/L_Frame_Stand_Alone.stl
Mercury_One/Vengeful/Standalone_Knob_Tensioners/stl/left_tensioner/L_Plate_3mm_No_Window(Optional).stl
Mercury_One/Vengeful/Standalone_Knob_Tensioners/stl/left_tensioner/L_Plate_6mm_Logo.stl
Mercury_One/Vengeful/Standalone_Knob_Tensioners/stl/left_tensioner/Left_Tensioner(Accent Color).stl
Mercury_One/Vengeful/Standalone_Knob_Tensioners/stl/right_tensioner/R_Frame_Stand_Alone.stl
Mercury_One/Vengeful/Standalone_Knob_Tensioners/stl/right_tensioner/R_Plate_3mm_No_Window(Optional).stl
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

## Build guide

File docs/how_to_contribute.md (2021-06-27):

# How to contribute

In order to contribute your mod or slicer profile you need to follow these steps:

1. Make sure you are logged into github (or create an account)
2. Go to [UserMods Repo](https://github.com/ZeroGDesign/UserMods)
3. Fork the repository
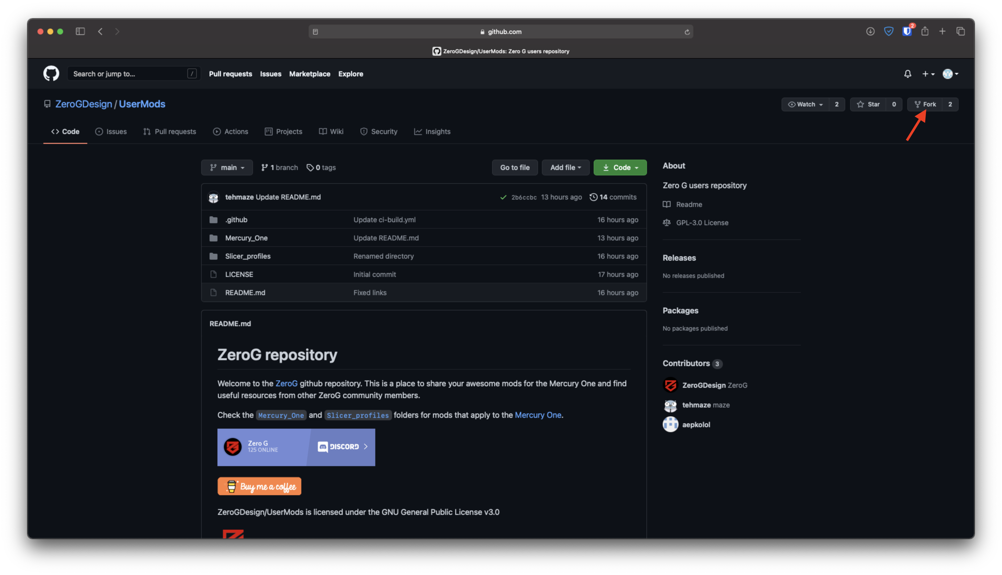
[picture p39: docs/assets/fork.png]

4. Upload your files to the right directory (make sure you are in the right repository)
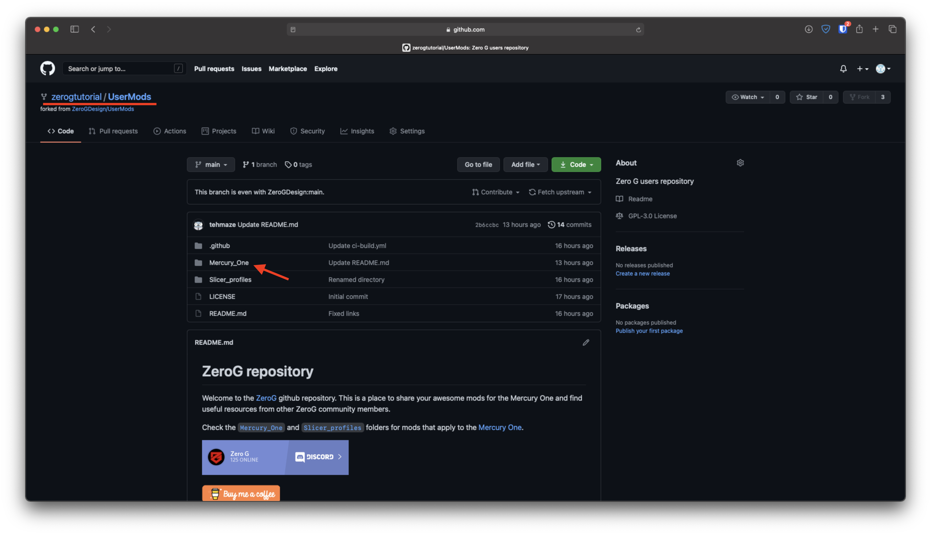
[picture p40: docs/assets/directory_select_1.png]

5. Add your files
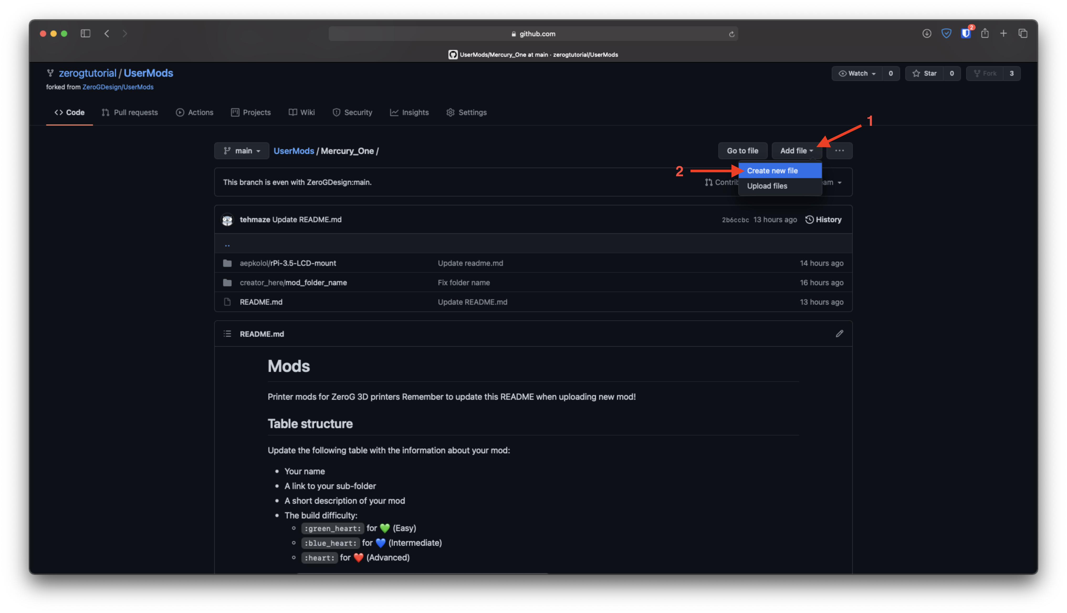
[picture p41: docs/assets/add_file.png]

	1. Click on `Add files`
	2. Click `Create new file`
6. Create a directory structure containing your nickname followed by `/` and mod name
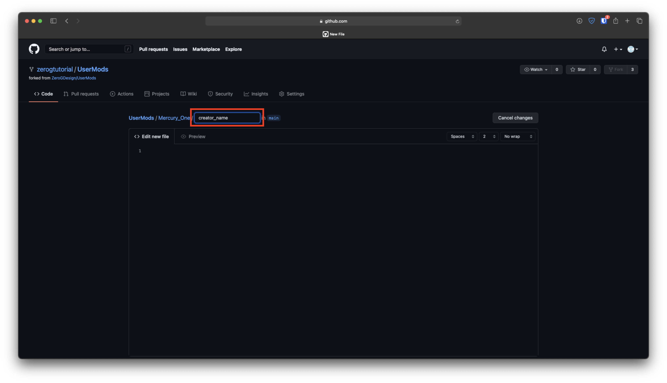
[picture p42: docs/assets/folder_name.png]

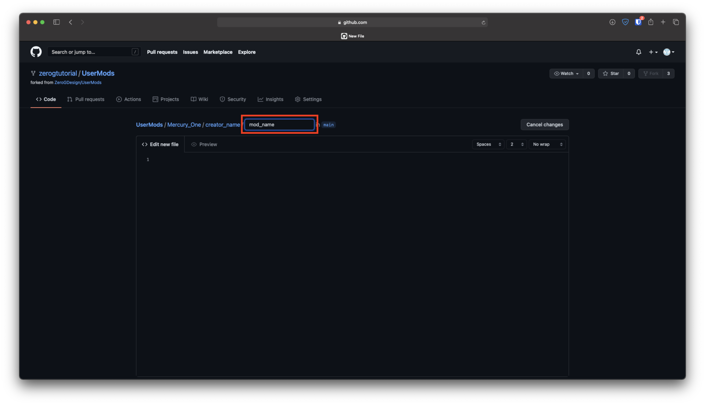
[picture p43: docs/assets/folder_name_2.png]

7. Drag and drop the file you want to upload (2), remember also to name it (1)
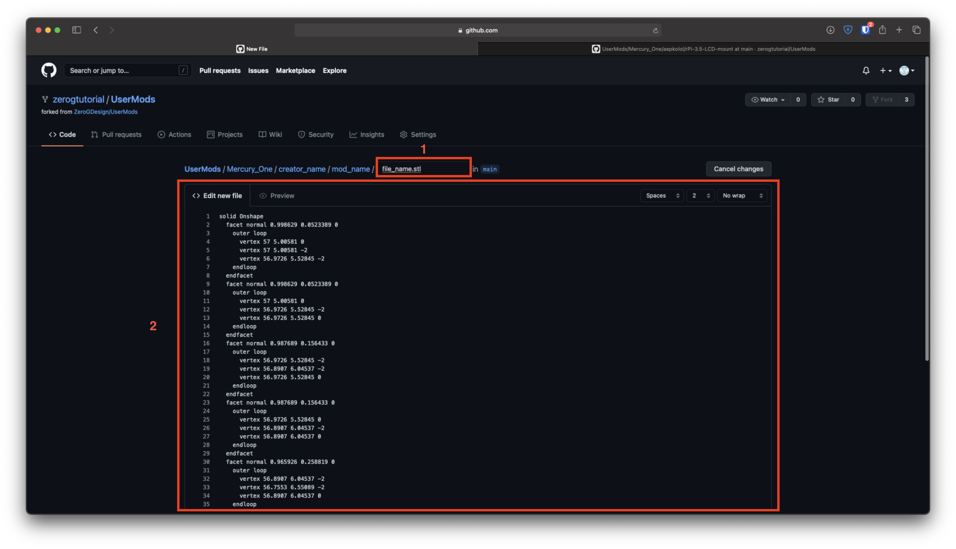
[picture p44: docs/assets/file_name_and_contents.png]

8. Commit the file
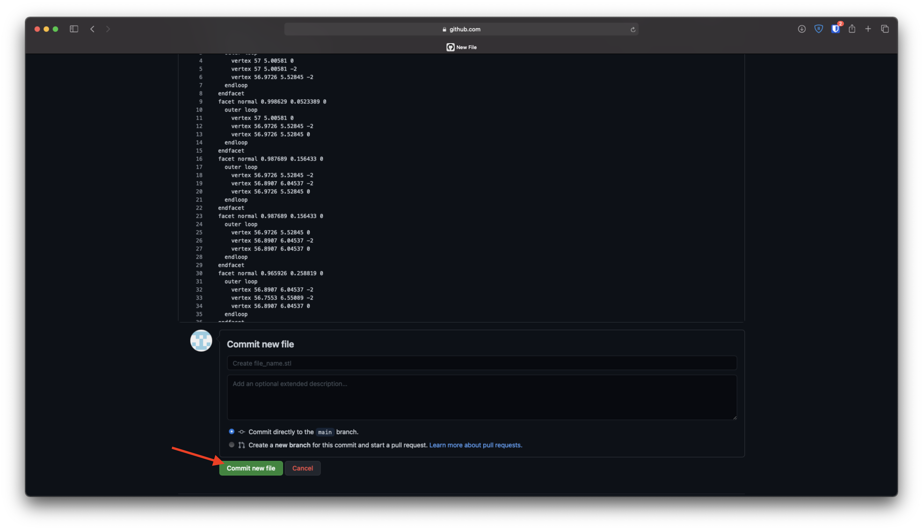
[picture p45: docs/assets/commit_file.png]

9. Edit `README.md` by adding your mod to the table (remember to commit the edited file!)
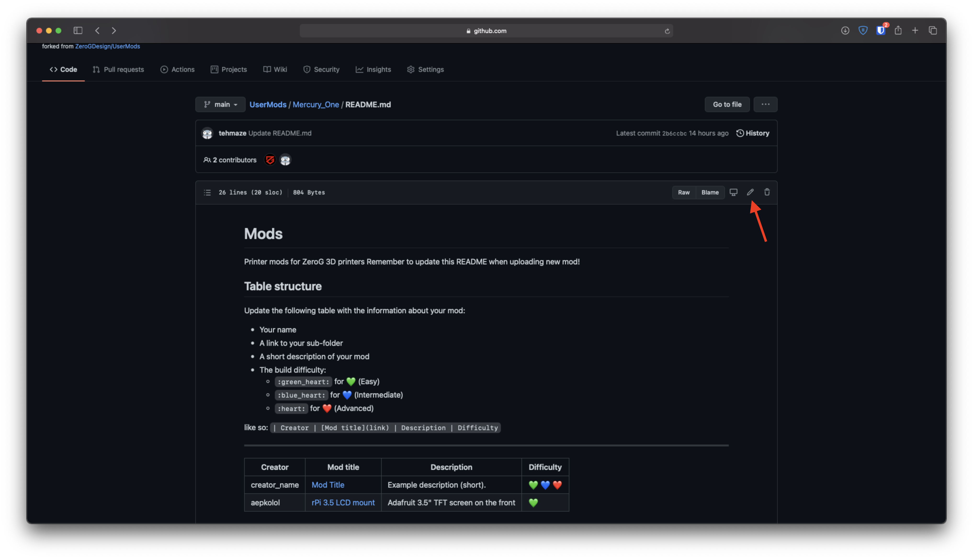
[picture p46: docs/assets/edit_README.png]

10. Go to Pull reqests section
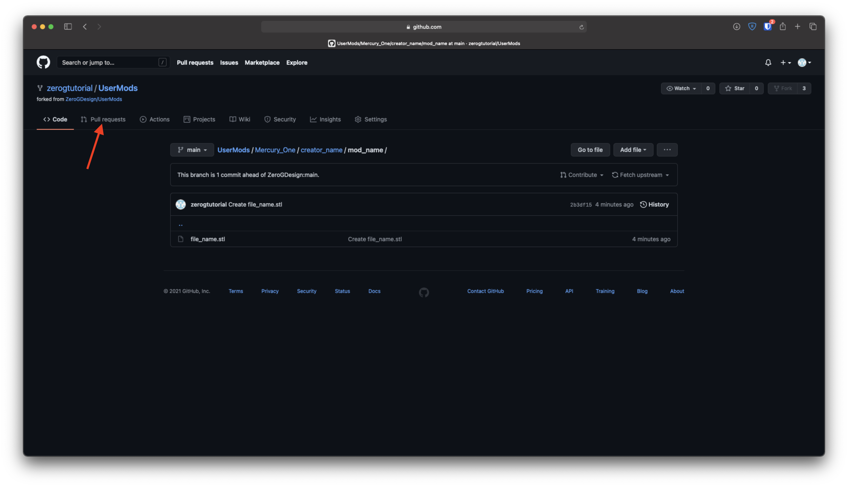
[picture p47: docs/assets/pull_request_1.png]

11. Click on `New pull request` button
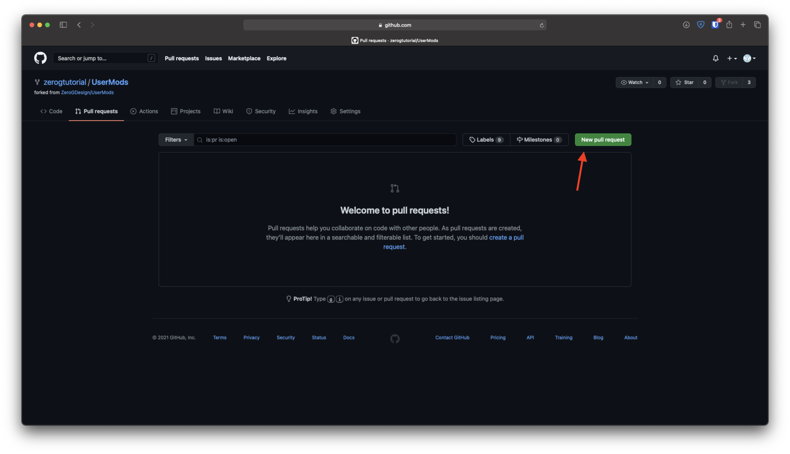
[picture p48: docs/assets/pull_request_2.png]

12. Make sure you are targetting a correct branch (1) and click on `Create pull request` (2)
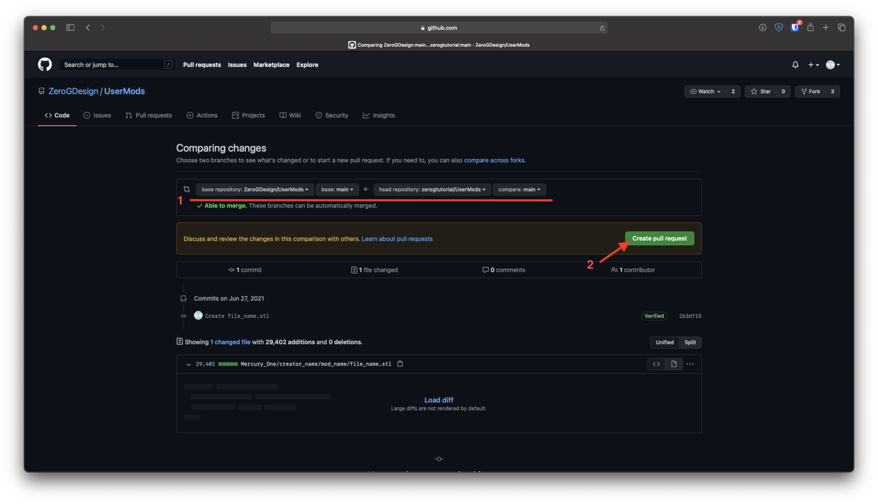
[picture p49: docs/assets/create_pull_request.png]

13. Wait for your request being approved and merged into UserMods repo

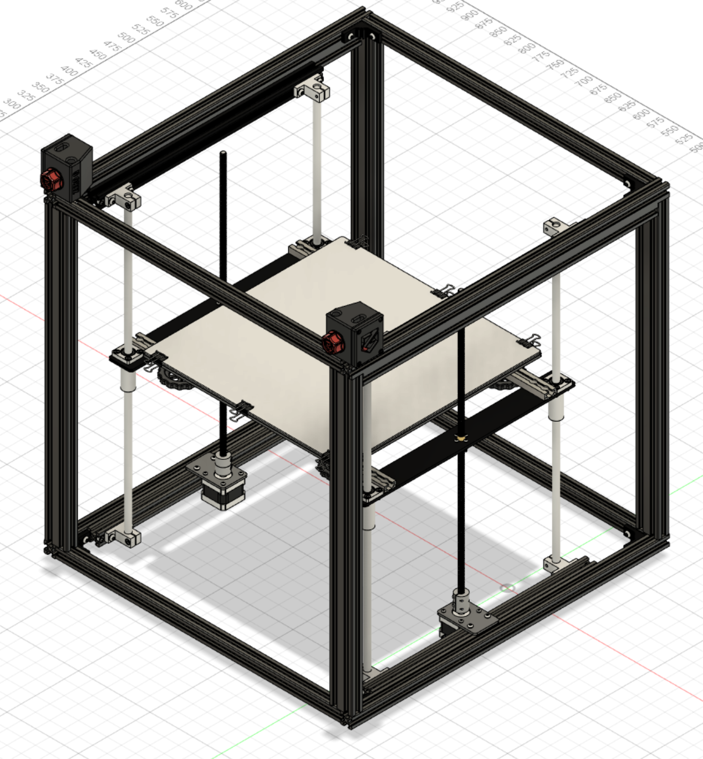
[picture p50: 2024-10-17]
Mercury_One/Vengeful/Standalone_Knob_Tensioners/images/Installed_View_E5_Plus.PNG

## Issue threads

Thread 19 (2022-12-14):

SAS ender 5 + zero g

Hobbss27, 2022-12-14:
i have been preparing to install this system and with the new update the duct seems to not line up fully.
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

also the mounting system will not work with my setup on the sides. it will work in the back( would be rather far) but i would rather have 1 per side. i plan to modify your mount to fit my printer. but as a reference with a stock bed.
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

nelsongraca, 2024-10-17:
stale

nelsongraca, 2024-10-17:
stale

Closed 2024-10-17.

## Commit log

2021-06-27 Added recommended directory structure
    [LCD Thinger.f3d, LCD Thinger.stl]
2021-06-27 Create stl
2021-07-21 Rename KW10 Bumpstop.step to EVA KW10 Bumpstop.step
    [EVA KW10 Bumpstop.step]
2021-07-21 Rename KW10 Endstop Mount.step to EVA KW10 Endstop Mount.step
    [EVA KW10 Endstop Mount.step]
2021-07-21 Rename [Endstop] Openbuilds Endstop v11.step to KW10 Enlarged Y Endstop Mount.step
    [KW10 Enlarged Y Endstop Mount.step]
2021-07-21 Rename EVA KW10 Bumpstop.step to EVA_KW10_Bumpstop.step
    [EVA_KW10_Bumpstop.step]
2021-07-21 Rename EVA KW10 Endstop Mount.step to EVA_KW10_Endstop_Mount.step
    [EVA_KW10_Endstop_Mount.step]
2021-07-21 Rename KW10 Enlarged Y Endstop Mount.step to KW10_Enlarged_Y_Endstop_Mount.step
    [KW10_Enlarged_Y_Endstop_Mount.step]
2021-09-10 Bertoo1337 ab shroud
    Mercury branded fan shroud for the Voron AfterBurner
    [FanShroud_Merc_logo.stl, Inlay C1.stl, Inlay C2.stl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]
2021-09-13 X extrusion squaring tool by Rudra (#10)
    Create X Extrusion Squaring Tool
    [X_Extrusion_Squaring_Tool x2.stl]
2021-11-10 Adding EVA mount and fan duct for Biqu H2 hotend/extruder
    [EVA-Biqu-H2-Faceplate.stl]
2021-12-10 Spool holder by Pizza boy
    [spoolholder_nut.STL, spoolholder_short.STL]
2022-05-23 Djsplice static cooling (#16)
    * Adding Static Cooling System files
    * Updated Readme
    * Fix relative links and spelling
    * Fix Fan Duct Link
    [Fan Bracket.stl, Fan Duct.stl, Fan Shroud.stl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]
2022-12-05 Scs shroud bracket updates (#18)
    [Fan Bracket.stl, Fan Duct.stl, Fan Shroud.stl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]
2022-12-05 Justinr54321 patch 1 (#15)
    [AB_EZABL_micro.stl]
2024-03-03 Wago Mount for 4 connectors (#26)
    * Create Wago4-Mount-Hydra
    * Delete Mercury_One/DrPeterPlastic/Wago4-Mount-Hydra
    * Wago Mount fpr Hydra Added
    * Update README.md
    [Wago4.step]
2024-10-17 Adding the Non-enclosure version of the Knob Tensioners (#22)
    * Create README.md
    * Add files via upload
    ---------
    [L_Frame_Stand_Alone.stl, L_Plate_3mm_No_Window(Optional).stl, L_Plate_6mm_Logo.stl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]
2024-10-17 New: gantry mgn9h parts (#25)
    * New: gantry mgn9h parts
    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
    [y-l-9.stl, y-r-9.stl]
2024-10-18 Add frame braces
    [AB_EZABL_micro.stl, Frame_Brace_M4_Zerog_Full.stl]
